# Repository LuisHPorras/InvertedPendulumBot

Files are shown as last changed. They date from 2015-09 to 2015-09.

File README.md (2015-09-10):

# InvertedPendulumBot

This project aims to be a platform to apply control and signal processing theory. Therefore basic and common algorithms has been used  such as PID and Complementary Filter and the following libraries helps the code to be clear and intelligible. Take a look at the [wiki] (https://github.com/LuisHPorras/InvertedPendulumBot/wiki)!

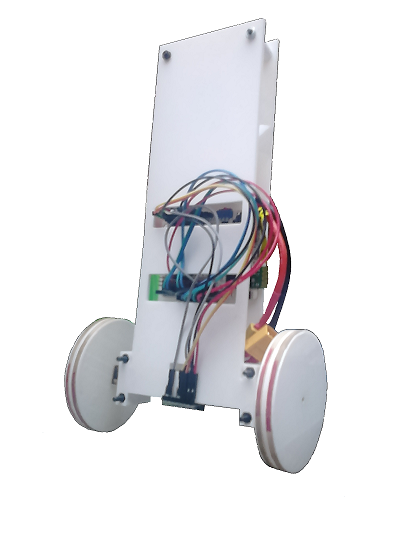
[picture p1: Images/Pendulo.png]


# License

InvertedPendulumBot is licensed under a [Creative Commons Attribution-ShareAlike 4.0 International License] (https://creativecommons.org/licenses/by-sa/4.0/)

Please read the [LICENSE] (../master/LICENSE.md) file for more details.

# Work in progress

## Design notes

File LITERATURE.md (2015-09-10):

# Similar projects

These are the projects I've been using as examples but there are lots of them and some may be better, so don't stop searching for them.

[Vertibot] (https://madebyfrutos.wordpress.com/2013/05/02/vertibot/)

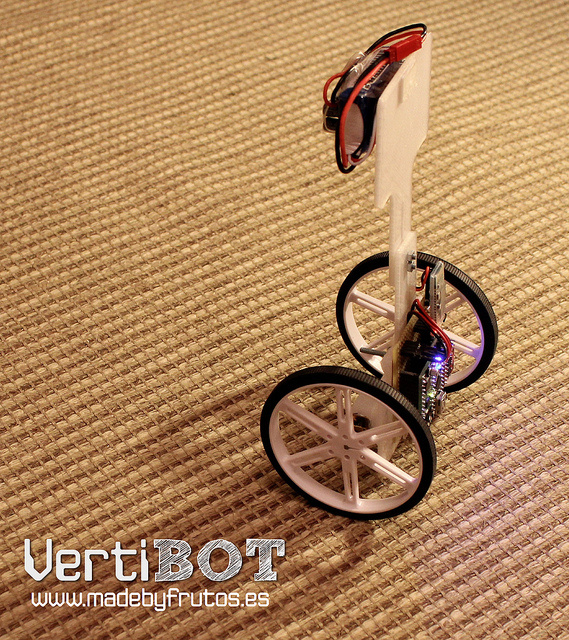
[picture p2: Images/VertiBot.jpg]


[Balanduino] ( http://blog.tkjelectronics.dk/2012/03/the-balancing-robot/)

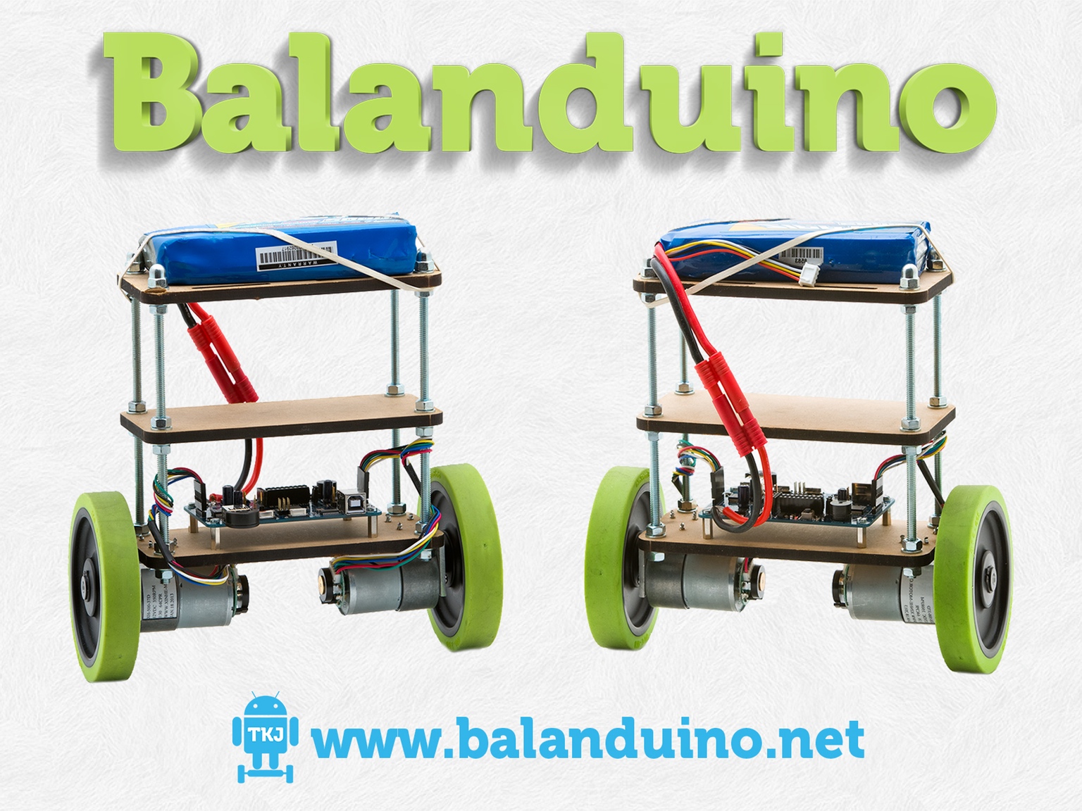
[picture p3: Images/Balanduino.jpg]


[ArduRoller] (http://makezine.com/projects/arduroller-self-balancing-robot/)

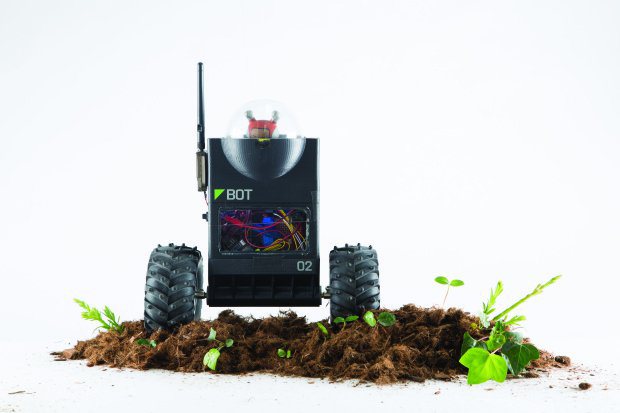
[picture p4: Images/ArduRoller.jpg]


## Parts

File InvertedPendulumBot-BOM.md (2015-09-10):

#Basic BOM 

Here I list the basic components I've used with a link to buy them and the datasheet when needed:

- [Arduino Uno](https://store.arduino.cc/product/A000066) or [bq ZUM] (http://www.bq.com/gb/placa-zum-bt)

- IMU 6DOF, accelerometer and gyroscope, [MPU-6050] (https://www.arduex.com/p937021-acelerometro-y-giroscopio-modelo-mpu-6050-gy-521.html), [Datasheet and Registers map] (http://www.invensense.com/products/motion-tracking/6-axis/mpu-6050/)

- 2 x Pololu [DC motors] () with planetary gear box (you can use anyone)

- H-bridge motor driver [A4990] (https://www.pololu.com/product/2137/resources), [Datasheet] (https://www.pololu.com/file/0J710/A4990-Datasheet.pdf)

- [LiPo Battery] (http://www.hobbyking.com/hobbyking/store/__7312__Rhino_1750mAh_2S_7_4v_20C_Lipoly_Pack.html) this one was extremely big for the robot

- Wires

- M3 screws and bolts (different lengths)

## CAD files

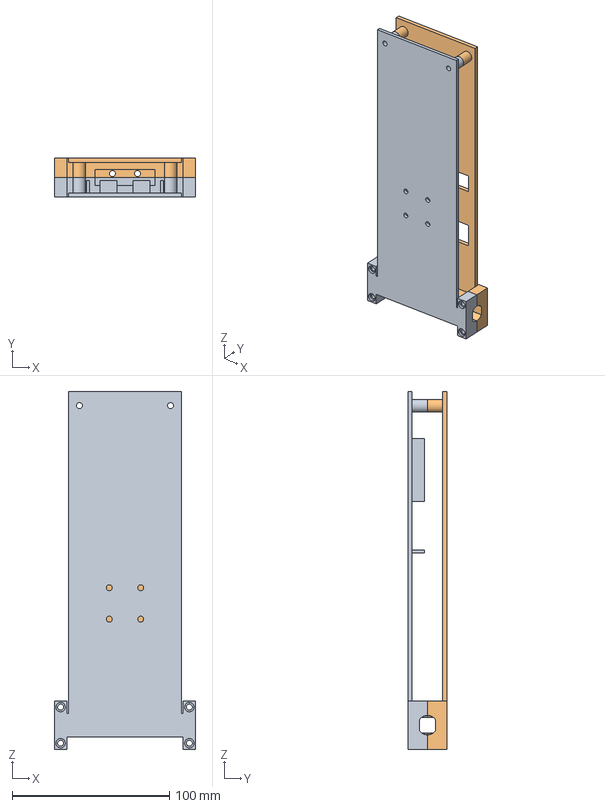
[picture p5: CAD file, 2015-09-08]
Design/Freecad/InvertedPendulumBot.fcstd
90.0 x 25.0 x 228.0 mm
[Difference]_Printable_Right
[Difference]_Printable_Left

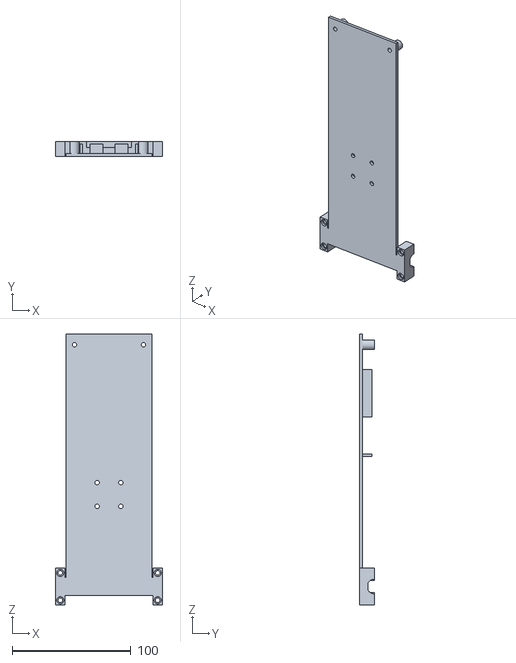
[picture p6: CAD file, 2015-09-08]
Design/STL/Right_Part.stl
90.0 x 12.5 x 228.0

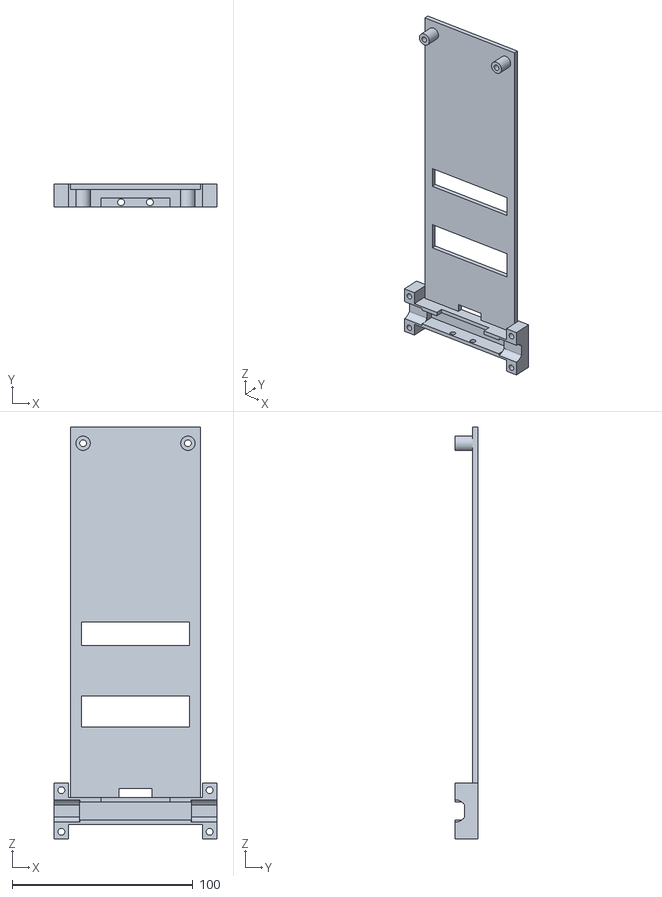
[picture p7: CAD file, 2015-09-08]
Design/STL/Left_Part.stl
90.0 x 12.5 x 228.0

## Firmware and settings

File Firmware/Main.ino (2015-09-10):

////////////////////////////////////////////////////
//
// Date: 16/08/15
// Author: Luis H. Porras
// 
// Inverted Pendulum Robot
// Description: Basic inverted pendulum robot based
// on different libraries such as MPU6050.h, PID.h, 
// Filter.h (which contains FilterOnePole.h) and Wire.h
// an Arduino library included in the IDE. 
// Building this robot will provide knowledge about
// signal processing ( Highpass and Lowpass filters
// combined to achieve a Complementary filter, Kalman
// filter etc.), control theory (PID controllers, 
// neural networks and genetic algorithms etc.),
// dynamical systems theory...
// Also contains comunications via bluetooth
//
// Code map:  
// This code has been divided in blocks that summerize 
// what is going on and what it is, almost all blocks
// are independet so if you comment one the code will
// work i.e., comment the comunication functions
// and the robot will run without Protocoder
// interface.
//
///////////////////////////////////////////////////


#include <Wire.h>
#include <MPU6050.h>
#include <FilterOnePole.h>
#include <PID_v1.h>

//Define motor pins
#define M11 10
#define M21 6
#define M12 9
#define M22 5
#define DRI 7

/////////////////////////////////////////////////////////////////
//                      Sensor variables                       //

MPU6050 mpu;
float apitch = 0, gpitch = 0; // Accelerometer pitch, apitch; Gyroscope Pitch, gpitch
float fapitch = 0, fgpitch = 0, fsignal = 0; // Filtered Accelerometer pitch, fapitch; Filtered Gyroscope Pitch, fgpitch
float sum, setZero;
int i;

/////////////////////////////////////////////////////////////////


/////////////////////////////////////////////////////////////////
//                        PID variables                        //

double Setpoint, Input, Output;
double Kp=80, Ki=18.3, Kd=0;//Ziegler-Nichols method Ku = 89, Tu=2.1; PID Kp=53.4 , Ki=50.86, Kd=14.2 noisy; PD Kp=71.2, Kd=18.7
PID myPID(&Input, &Output, &Setpoint, Kp, Ki, Kd, DIRECT);

// Timers
unsigned long timer = 0;
float timeStep = 0.01;

/////////////////////////////////////////////////////////////////

/////////////////////////////////////////////////////////////////
//                          DC Motors                          //

int offset = 3;

/////////////////////////////////////////////////////////////////
  
/////////////////////////////////////////////////////////////////
//                        Communications                        //

// Command id's                            
const unsigned char CMD_STOP = 'S';   
const unsigned char CMD_PLAY = 'P';
const unsigned char CMD_FORD = 'F';
const unsigned char CMD_BACK = 'B';
const unsigned char CMD_STAY = 'Y'; 
const unsigned char CMD_PLUS = 'I';
const unsigned char CMD_MINUS = 'O';
const unsigned char CMD_KP = 'T';
const unsigned char CMD_KI = 'E';
const unsigned char CMD_KD = 'D';  
const char CMD_END = '\r';   // Character end of frame \r is chosen for working with gtkterm correctly in Linux. If the arduino terminal is used, select the option "carriage return"                          

// Command receiver state
const int WAITING_CMD_ID = 1;
const int WAITING_END = 2;
int state = WAITING_CMD_ID; // Initial state

//Command manage
String inputString = "";        // A string to hold incoming data
int cmd;
bool cmd_ok = false;

bool play = false;
int constantSelector = 1; // 1->Kp, 2->Ki, 3->Kd

/////////////////////////////////////////////////////////////////


void setup() 
{
  Serial.begin(19200);

  /////////////////////////////////////////////////////////////////
  //                        BT communications                    //
  
  // Get and execute the commands
  while(play == false)
  {
    getCommands();
    Serial.println("Waiting start...");
    delay(100);
  }
  Serial.println("Bluethooh connected");

  /////////////////////////////////////////////////////////////////

  /////////////////////////////////////////////////////////////////
  //                      Initialize MPU6050                     //

  while(!mpu.begin(MPU6050_SCALE_250DPS, MPU6050_RANGE_2G))
  {
    Serial.println("Could not find a valid MPU6050 sensor, check wiring!");
    delay(500);
  }

  // Calibrate gyroscope. The calibration must be at rest.
  // If you don't want calibrate, comment this line.
  mpu.calibrateGyro();
        
  for( i=0; i<10; i++){
      
    Vector normAccel = mpu.readNormalizeAccel();
    sum += (atan2(normAccel.XAxis, sqrt(normAccel.YAxis*normAccel.YAxis + normAccel.ZAxis*normAccel.ZAxis))*180.0)/M_PI; // Signe '-' in this operation has been deleted because of the position of the IMU
          
  }
        
  setZero = sum / i;

  /////////////////////////////////////////////////////////////////
    
  /////////////////////////////////////////////////////////////////
  //                         PID settings                        //
    
  Setpoint = 0;
  myPID.SetOutputLimits(-255, 255);
  myPID.SetSampleTime(15);
  myPID.SetMode(AUTOMATIC);
    
  /////////////////////////////////////////////////////////////////
     
  /////////////////////////////////////////////////////////////////
  //                         DC Motors                           //   
    
  digitalWrite(DRI, HIGH);
  motorWrite(M11, M12, 0, 0);
  motorWrite(M21, M22, 0, 0);
  
  /////////////////////////////////////////////////////////////////
    
}

void loop()
{
  if(play == true)
  {
    timer = millis();

    /////////////////////////////////////////////////////////////////
    //                Data adquisition and filtering               //

    // Read normalized values
    Vector normAccel = mpu.readNormalizeAccel();
    Vector norm = mpu.readNormalizeGyro();

    // Calculate angle
    apitch = (atan2(normAccel.XAxis, sqrt(normAccel.YAxis*normAccel.YAxis + normAccel.ZAxis*normAccel.ZAxis))*180.0)/M_PI; // Signe '-' in this operation has been deleted because of the position of the IMU
    gpitch = norm.YAxis * timeStep;

    fsignal = 0.98 * (fsignal + gpitch) + 0.02 * (apitch-setZero);

    /////////////////////////////////////////////////////////////////

    /////////////////////////////////////////////////////////////////
    //                        Calculate PID                        //

    Input = fsignal;
    myPID.Compute();

    //Serial.print(Output);
    //Serial.print("\n");

    /////////////////////////////////////////////////////////////////

    /////////////////////////////////////////////////////////////////
    //                           Write Output                      //

      if( Output < -10 && Input < 45)
      {
        digitalWrite(DRI, HIGH);
        motorWrite(M11, M12, 0, (int)-Output - offset);
        motorWrite(M21, M22, 1, (int)-Output);
      }
      else if ( Output > 10 && Input > -45)
      {
          digitalWrite(DRI, HIGH);
        motorWrite(M11, M12, 1, (int)Output - offset);
        motorWrite(M21, M22, 0, (int)Output);
      }
      else
      {
        digitalWrite(DRI, LOW);
      }

    /////////////////////////////////////////////////////////////////

    /////////////////////////////////////////////////////////////////
    //                          Debug                              //

    //Serial.print(Input);
    //Serial.print(" ");
    //Serial.print((int)Output);
    //Serial.print("\n");
      
    /////////////////////////////////////////////////////////////////

    /////////////////////////////////////////////////////////////////
    //                   Protocoder communications                 //
    getCommands();
    //Serial.println(play);
    /////////////////////////////////////////////////////////////////
    
    delay((timeStep*1000) - (millis() - timer)); //Sensor Time Step
  }
  else
  {
    /////////////////////////////////////////////////////////////////
    //                   Protocoder communications                 //
    getCommands();
    //Serial.println(play);
    /////////////////////////////////////////////////////////////////
    
  }  
}

/////////////////////////////////////////////////////////////////
//                          Functions                          //


void motorWrite(int P1, int P2, int dir, int vel)
{
  if(dir == 1)
  {
    digitalWrite(P1, LOW);
    analogWrite(P2, 255 - vel);
  }
  else 
  {
    digitalWrite(P2, HIGH);
    analogWrite(P1, vel);
  }
  
}

void changeConstant(bool add, int selector)
{
  if(add)
  {
    if(selector == 1)
      Kp += 5;
    else if(selector == 2)
      Ki += 1;
    else
      Kd += 1;
  }
  else
  {
    if(selector == 1)
      Kp -= 5;
    else if(selector == 2)
      Ki -= 1;
    else
      Kd -= 1;
  }
  if(Kp == 0)
  {
     motorWrite(M11, M12, 0, 0);
     motorWrite(M21, M22, 0, 0);
  }
  myPID.SetTunings(Kp, Ki, Kd);
    
}

void getCommands()
{
  //Serial.println("getCommands");
  
  // Read the incoming commands
  while (Serial.available())
  {
    // Read the received char
    char inChar = (char)Serial.read();
     
    // Depending on the state
    switch(state)
    {    
      // Read the cmd ID
      case WAITING_CMD_ID:
      
         //inputString = "";
         cmd = inChar;
           
         // The next state depends on the command id
         switch(cmd)
         {
           case CMD_STOP:
           case CMD_PLAY:
           case CMD_FORD:
           case CMD_BACK:
           case CMD_STAY:
           case CMD_PLUS:
           case CMD_MINUS:
           case CMD_KP:
           case CMD_KI:
           case CMD_KD:
             state = WAITING_END;
             //Serial.println("Waiting end");
             break;
                
           // If the command is unknow, move to the initial state  
           default:
             state = WAITING_CMD_ID;
             Serial.println("Wrong command");
         }
         break;  
         
       // Read the end of the frame
       case WAITING_END:
         
         // The next state is the initial, in any case
         state = WAITING_CMD_ID;
         
         // End of frame received correctly
         if (inChar == CMD_END) {
           cmd_ok = true;             // The command is ok!
           Serial.println("Command received");
           runCommand();
         }  
         else {
           cmd_ok = false;   // Invalid frame. It will be ignored
         }
         break;
          
    } // End switch
      
  } // End While
    
}

void runCommand()
{
  // If the frame received is ok... process!
  if (cmd_ok)
  {
    //Serial.println("OK");
    switch(cmd)
    {  
      // Command play
      case CMD_PLAY:
        play = true;
        break;
        
      // Command stop
      case CMD_STOP:
        play = false;
        motorWrite(M11, M12, 0, 0);
        motorWrite(M21, M22, 0, 0);
        break;

      // Command move fordward Setpoint
      case CMD_FORD:
        Setpoint += 0.05;
        break;

      // Command move backward Setpoint
      case CMD_BACK:
        Setpoint -= 0.05;
        break;

      // Command set Setpoint to 0
      case CMD_STAY:
        Setpoint = 0;
        break;

      // Command add to a selected constant
      case CMD_PLUS:
        changeConstant(1, constantSelector);
        break;
        
      // Command extract to a selected constant
      case CMD_MINUS:
        changeConstant(0, constantSelector);
        break;

      // Command select kp
      case CMD_KP:
        constantSelector = 1;
        break;

      // Command select ki
      case CMD_KI:
        constantSelector = 2;
        break;

      // Command select kd
      case CMD_KD:
        constantSelector = 3;
        break;

    }
    
    cmd_ok = false;
  }  
}
/////////////////////////////////////////////////////////////////

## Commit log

2015-09-08 Desing without wheels
    [InvertedPendulumBot.fcstd, Left_Part.stl, Right_Part.stl]
2015-09-10 Create BOM
